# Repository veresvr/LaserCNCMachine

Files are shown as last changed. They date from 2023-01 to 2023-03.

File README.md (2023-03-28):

# Laser CNC Machine

This machine is not something special, just DIY.
Firstly I planned to use a laser but its so easy, so I decided to build milling carriage, like [this](https://github.com/veresvr/SpindleCarriageForCNC).
Also here is [Control Box](https://github.com/veresvr/CNC-Control-Box) for it.<br>
BOM and drawings for the machine [here](https://github.com/veresvr/LaserCNCMachine/tree/main/ProductionFiles/LaserCNCMachine.pdf).



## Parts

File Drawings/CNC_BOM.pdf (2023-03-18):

| Project CNC machine Project Link GitHub (https://github.com/veresvr/LaserCNCMachine) Title cnc_laser_v1.0.SLDASM Project Number CNC.00.00 Designer Vladimir Tyrkin Drawn by Vladimir Tyrkin File CNC_BOM.xlsx Date 18 March 2023
Dwg. | Item No. | Qty | Description | Material | Manufacturer | Part Number | Manufacturer Link | Weight | Total Weight
CNC.01.01 | | 3 | Structural Aluminum Profile 2040 | 6063-T5 | McMaster-Carr | 5537T111-5537T107 | McMaster-Carr (https://www.mcmaster.com/5537T111-5537T107/) | 346 | 1038
| | | | | Soberizavod | 224SHX | Soberizavod (https://www.soberizavod.ru/catalog/seriya_20_obychnyy_paz/profil_konstruktsionnyy_20kh40sh_bez_pokrytiya/)
CNC.01.11 | | 2 | Structural Aluminum Profile 2020 | 6063-T5 | McMaster-Carr | 5537T514-5537T751 | McMaster-Carr (https://www.mcmaster.com/5537T514-5537T751/) | 169 | 338
| | | | | Soberizavod | 222SHX | Soberizavod (https://www.soberizavod.ru/catalog/seriya_20_obychnyy_paz/profil_konstruktsionnyy_20kh20sh_bez_pokrytiya/)
CNC.01.21 | | 1 | Frame Base Y | 6063-T5 | McMaster-Carr | 4630T124 | McMaster-Carr (https://www.mcmaster.com/4630T124/) | 43.77 | 43.77
CNC.01.22-1 | | 1 | Frame Base Mount Bracket Y Without Hole | 6061 Alloy | McMaster-Carr | 9146T14-9146T141 | McMaster-Carr (https://www.mcmaster.com/9146T14-9146T141/) | 7.97 | 7.97
CNC.01.22-2 | | 1 | Frame Base Mount Bracket Y With Hole | 6061 Alloy | McMaster-Carr | 9146T14-9146T142 | McMaster-Carr (https://www.mcmaster.com/9146T14-9146T141/) | 7.9 | 7.9
CNC.02.25 | | 4 | Threaded Rod | Alloy Steel | McMaster-Carr | 94595A235 | McMaster-Carr (https://www.mcmaster.com/94595A235/) | 2.16 | 8.64
CNC.01.02-1 | | 2 | Foot | Polycarbonate Sheet | McMaster-Carr | 8574K281 | McMaster-Carr (https://www.mcmaster.com/8574K281/) | 32.67 | 65.34
CNC.01.02-2 | | 1 | Foot | Polycarbonate Sheet | McMaster-Carr | 8574K281 | McMaster-Carr (https://www.mcmaster.com/8574K281/) | 32.67 | 32.67
CNC.01.02-3 | | 1 | Foot | Polycarbonate Sheet | McMaster-Carr | 8574K281 | McMaster-Carr (https://www.mcmaster.com/8574K281/) | 30.39 | 30.39
CNC.02.42 | | 1 | Adjustment Equipment Part | Polycarbonate Sheet | McMaster-Carr | 8574K281 | McMaster-Carr (https://www.mcmaster.com/8574K281/) | 73.78 | 73.78
CNC.02.41 | | 1 | Stepper Side Part | Polycarbonate Sheet | McMaster-Carr | 8574K281 | McMaster-Carr (https://www.mcmaster.com/8574K281/) | 67.72 | 67.72
CNC.02.44 | | 1 | Equipment Adapter | Polycarbonate Sheet | McMaster-Carr | 8574K281 | McMaster-Carr (https://www.mcmaster.com/8574K281/) | 51.48 | 51.48
CNC.02.21 | | 1 | Right Side Base | Polycarbonate Sheet | McMaster-Carr | 8574K281 | McMaster-Carr (https://www.mcmaster.com/8574K281/) | 99.76 | 99.76
CNC.02.31 | | 1 | Left Side Base | Polycarbonate Sheet | McMaster-Carr | 8574K281 | McMaster-Carr (https://www.mcmaster.com/8574K281/) | 104.4 | 104.4
CNC.02.22 | | 8 | Wheel Spacer 1 | 6061-T6 (SS) | McMaster-Carr | 4634T36 | McMaster-Carr (https://www.mcmaster.com/4634T36/) | 1.12 | 8.96
CNC.01.31 | | 4 | Corner For Sensor | 6060 Alloy | McMaster-Carr | 5585N13-5585N117 | McMaster-Carr (https://www.mcmaster.com/5585N13-5585N117/) | 2.49 | 9.96
CNC.02.24 | | 2 | Corner Bracket For Cable Chain | 6060 Aluminum | McMaster-Carr | 5585N19-5585N137 | McMaster-Carr (https://www.mcmaster.com/5585N19-5585N137/) | 5 | 10
CNC.02.43 | | 8 | Wheel Spacer 2 | 6061-T6 (SS) | McMaster-Carr | 4634T36 | McMaster-Carr (https://www.mcmaster.com/4634T36/) | 1.37 | 10.96
CNC.02.51 | | 1 | Frame Base X | 6063-T5 | McMaster-Carr | 4630T124 | McMaster-Carr (https://www.mcmaster.com/4630T124/) | 17.7 | 17.7
CNC.02.52 | | 1 | Frame Base Mount Bracket X | 6061 Alloy | McMaster-Carr | 9146T15-9146T151 | McMaster-Carr (https://www.mcmaster.com/9146T15-9146T151/) | 6.75 | 6.75
CNC.02.60 | | 1 | Equipment Cable Carrier | Nylon | Aliexpress | none | Aliexpress (https://aliexpress.ru/item/32737987887.html?_ga=2.220930584.1029082422.1628014899-) | 21.86 | 21.86
CNC.03.00 | | 1 | Cable Carrier | Nylon | Aliexpress | none | Aliexpress (https://aliexpress.ru/item/32737987887.html?_ga=2.232483359.1029082422.1628014899-) | 21.86 | 21.86
CNC.04.05-1 | | 1 | Cable label X | Acrylic | Aliexpress | none | Aliexpress (https://aliexpress.ru/item/1005002110837854.html?sku_id=12000018773424358) | 1.58 | 1.58
CNC.04.05-2 | | 1 | Cable label Y | Acrylic | Aliexpress | none | Aliexpress (https://aliexpress.ru/item/1005002110837854.html?sku_id=12000018773424358) | 1.58 | 1.58
CNC.04.05-4 | | 1 | Cable label PWR | Acrylic | Aliexpress | none | Aliexpress (https://aliexpress.ru/item/1005002110837854.html?sku_id=12000018773424358) | 1.58 | 1.58
CNC.04.05-5 | | 1 | Cable label DATA | Acrylic | Aliexpress | none | Aliexpress (https://aliexpress.ru/item/1005002110837854.html?sku_id=12000018773424358) | 1.58 | 1.58
CNC.05.01-1 | | 2 | T-slot Table Plate | 6105 Alloy | Soberizavod | TL1 | Soberizavod (https://www.soberizavod.ru/catalog/profil_dlya_stola_anodirovannyj/profil_dlya_stola_legkiy_11kh75_an_serebro/) | 541.63 | 1083.3
CNC.05.01-2 | | 2 | T-slot Table Plate | 6105 Alloy | Soberizavod | TL1 | Soberizavod (https://www.soberizavod.ru/catalog/profil_dlya_stola_anodirovannyj/profil_dlya_stola_legkiy_11kh75_an_serebro/) | 541.8 | 1083.6
CNC.05.01-3 | | 1 | T-slot Table Plate | 6105 Alloy | Soberizavod | TL1 | Soberizavod (https://www.soberizavod.ru/catalog/profil_dlya_stola_anodirovannyj/profil_dlya_stola_legkiy_11kh75_an_serebro/) | 377.6 | 377.6
CNC.05.05 | | 2 | Corner Braket Long | 6061 Alloy | McMaster-Carr | 5585N18-5585N134 | McMaster-Carr (https://www.mcmaster.com/5585N18-5585N134/) | 117.04 | 234.08
CNC.02.11 | | 1 | Rotary Shaft | AISI 1020 | McMaster-Carr | 8920K18-8920K183 | McMaster-Carr (https://www.mcmaster.com/8920K18-8920K183/) | 61.66 | 61.66
None | | 4 | Corner Bracket 40х20L | AISI 1035 Steel (SS) | Soberizavod | H49 | Soberizavod (https://www.soberizavod.ru/catalog/uglovye_soediniteli_seriya_20/ugolok_40kh20l_paz_6_h49/) | 49 | 196
None | | 8 | Corner Bracket 20х20L | Steel | Soberizavod | none | Soberizavod (https://www.soberizavod.ru/catalog/uglovye_soediniteli_seriya_20/ugolok_20kh20l_paz_6_m51/) | 10.14 | 81.12
| | | | Anodized 6063 Aluminum | McMaster-Carr | 5537T935 | McMaster-Carr (https://www.mcmaster.com/5537T935/)
None | | 1 | LASER 5500mW | Multimaterial | Aliexpress | none | Aliexpress (https://aliexpress.ru/item/32807131516.html?mp=1&_ga=2.210714258.625657640.1626994396-) | 400 | 400
None | | 4 | Limit Switch | Multimaterial | DIGIKEY | none | DIGIKEY (https://www.digikey.com/en/products/detail/omron-electronics-inc-emc-div/ssg-01l2t-5/3102941) | 1.6 | 6.4
| | | | Multimaterial | Aliexpress | none | Aliexpress (https://aliexpress.ru/item/32820271171.html?_ga=2.96440341.847069604.1626648373-)
None | | 2 | Nema 17HS4401 Stepper Motor | Multimaterial | Aliexpress | none | Aliexpress (https://aliexpress.ru/item/32665922113.html?_ga=2.134133639.847069604.1626648373-) | 315 | 630
None | | 12 | Cable Tie Plastic | Nylon 101 | McMaster-Carr | 7130K12 | McMaster-Carr (https://www.mcmaster.com/7130K12/) | 0.18 | 2.16
None | | 3 | Timing Belt 430mm | Rubber | Aliexpress | none | Aliexpress (https://aliexpress.ru/item/32619587350.html?_ga=2.189989419.1029082422.1628014899-) | 3.98 | 11.94
| | | Timing Belt 430mm | Rubber | McMaster-Carr | 3682N1-3682N13 | McMaster-Carr (https://www.mcmaster.com/3682N1-3682N13/)
None | | 3 | GX16-4P cable female | Multimaterial | Aliexpress | none | Aliexpress (https://aliexpress.ru/item/32776129751.html?_ga=2.152725433.1029082422.1628014899-) | 10 | 30
None | | 3 | Pulley GT2-12 | Multimaterial | Aliexpress | none | Aliexpress (https://aliexpress.ru/item/32871142006.html?_ga=2.137935673.847069604.1626648373-) | 1.23 | 3.69
Page 1 of 2 | 3/18/2023 14:22

Dwg. | Item No. | Qty | Description | Material | Manufacturer | Part Number | Manufacturer Link
Weight

Total
Weight
None | 1 | Flexible shaft coupling 5x5 | Multimaterial | Aliexpress | none | Aliexpress (https://aliexpress.ru/item/32619555244.html?_ga=2.139041594.847069604.1626648373-) | 16.06 | 16.06
None | 1 | Connector D-SUB 9 Male | Multimaterial | MOUSER | none | Mouser (https://eu.mouser.com/ProductDetail/HARTING/09641227230?qs=qa49y27LPCEuVI2dYdFOjA%3D%3D) | 5 | 5
None | 1 | Connector PG11 | ABS | Amazon | none | Amazon (https://www.amazon.com/White-Plastic-Waterproof-Glands-Connectors/dp/B00843UH4O) | 12.38 | 12.38
None | 1 | Cable Holder | ABS | Soberizavod | none | Soberizavod (https://www.soberizavod.ru/catalog/zaglushki_dlya_paza/zaglushka_dlya_paza_6_mm_chernaya_z15/) | 3.07 | 3.07
None | 1 | Heat-Shrink Tubing 1 (Length 110mm) | Rubber | Digikey | ATU031K-ND | Digikey (https://www.digikey.com/en/products/detail/te-connectivity-raychem-cable-protection/ATUM-3-1-0-STK/573461) | 0 | 0
None | 1 | Heat-Shrink Tubing 2 (Length 25mm) | Rubber | Digikey | SCT-NO.2-E5-0-12MMND | Digikey (https://www.digikey.com/en/products/detail/te-connectivity-raychem-cable-protection/SCT-NO-2-E5-0-12MM/5318099) | 0 | 0
Total weight | 6322.2

3D printed parts

CNC.02.23 | 1 | Spacer for stepper | PET-G | McMaster-Carr | 3462N1 | McMaster-Carr (https://www.mcmaster.com/3462N1/) | 20.9 | 20.9
| | File: ProductionFiles/SpacerForStepper.STL
CNC.02.45 | 2 | Carriage Spacer | PET-G | McMaster-Carr | 3462N1 | McMaster-Carr (https://www.mcmaster.com/3462N1/) | 5.49 | 10.98
| | File: ProductionFiles/CarriageSpacer.STL
Total weight | 31.88
Screws
None | 4 | Head screw ISO 7380 M5 x 50 | AISI 304 | Aliexpress | none | Aliexpress (https://aliexpress.ru/item/32966917947.html?_ga=2.131725446.847069604.1626648373-) | 8.84 | 35.36
None | 56 | M3 NYLOC DIN 985 | AISI 304 | Aliexpress | 500214 | Aliexpress (https://www.mcmaster.com/nuts/locknuts/metric-18-8-stainless-steel-nylon-insert-locknuts/) | 0.4 | 22.4
None | 6 | Square nut M5 | Zinc-Plated Steel | Soberizavod | A209 | Soberizavod (https://www.soberizavod.ru/catalog/sukhari_pazovye_paz_6/sukhar_pazovyy_ploskiy_m5_paz_6_a209/) | 1.84 | 11.04
| | | Zinc-Plated Steel | McMaster-Carr | 5537t161 | McMaster-Carr (https://www.mcmaster.com/5537t161/)
None | 20 | M5 NYLOC DIN 985 | AISI 304 | McMaster-Carr | 5100214 | McMaster-Carr (https://www.mcmaster.com/nuts/locknuts/metric-18-8-stainless-steel-nylon-insert-locknuts/) | 1.1 | 22
None | 4 | Low Profile Hex Screw M5x30 | Alloy Steel | Aliexpress | none | Aliexpress (https://aliexpress.ru/item/4001232036314.html?_ga=2.27484988.1065263870.1623483208-) | 5.27 | 21.08
| | | Alloy Steel | McMaster-Carr | none | McMaster-Carr (https://www.mcmaster.com/90358A119/)
None | 8 | Head screw ISO 7380 M5 x 35 | AISI 304 | Aliexpress | none | Aliexpress (https://aliexpress.ru/item/32966917947.html?_ga=2.9302450.625657640.1626994396-) | 5.08 | 40.64
None | 6 | Head screw ISO 7380 M5 x 6 | 18-8 Stainless Steel | Aliexpress | none | Aliexpress (https://aliexpress.ru/item/32966917947.html?_ga=2.159815732.847069604.1626648373-) | 2 | 12
None | 20 | ISO 10642 - M3 x 16 - 16N | 18-8 Stainless Steel | McMaster-Carr | none | McMaster-Carr (https://www1.mcmaster.com/screws/flat-head-screws/phillips-flat-head-screws/metric-18-8-stainless-steel-phillips-flat-head-screws/) | 0.47 | 9.4
None | 24 | Head screw ISO 7380 M5 x 8 | 18-8 Stainless Steel | McMaster-Carr | 91292A121 | McMaster-Carr (https://www.mcmaster.com/94500A230/) | 2 | 48
| | | 18-8 Stainless Steel | Aliexpress | none | Aliexpress (https://aliexpress.ru/item/32953923124.html?_ga=2.138868666.847069604.1626648373-)
None | 16 | Washer DIN 125 - A 5.3 | Zinc Plated Steel | McMaster-Carr | 91166A240 | McMaster-Carr (https://www1.mcmaster.com/91166A240/) | 0.44 | 7.04
None | 32 | T nut 2020 М5 | 316 Stainless Steel | Aliexpress | none | Aliexpress (https://aliexpress.ru/item/32955951597.html?spm=a2g0s.9042311.0.0.274233ed1qtpPS) | 2.08 | 66.56
None | 4 | Washer DIN 125 - A 3.2 | Zinc Plated Steel | McMaster-Carr | 91166A210 | McMaster-Carr (https://www1.mcmaster.com/91166A210/) | 0.12 | 0.48
None | 14 | ISO 4762 M3 x 8 - 8N | Zinc Plated Steel | McMaster-Carr | 91502A103 | McMaster-Carr (https://www.mcmaster.com/91502A103/) | 0.8 | 11.2
None | 14 | ISO 4762 M3 x 12 - 12N | 18-8 Stainless Steel | McMaster-Carr | none | McMaster-Carr (https://www.mcmaster.com/screws/socket-head-screws/socket-head-screws-6/18-8-stainless-steel-socket-head-screws-11/system-of-measurement~metric/) | 1.16 | 16.24
None | 8 | ISO 7380 - M5 x 10 - 10N | 316 Stainless Steel | McMaster-Carr | 90943A117 | McMaster-Carr (https://www.mcmaster.com/90943A117/) | 2.09 | 16.72
None | 4 | ISO 7380 - M5 x 16 - 16N | 18-8 Stainless Steel | McMaster-Carr | 92095A212 | McMaster-Carr (https://www.mcmaster.com/92095A212/) | 2.9 | 11.6
None | 16 | ISO 7380 - M3 x 8 - 8N | 18-8 Stainless Steel | McMaster-Carr | 92095A181 | McMaster-Carr (https://www1.mcmaster.com/92095A181/) | 0.6 | 9.6
None | 12 | ISO 4762 M6 x 20 - 20N | Zinc-Plated Steel | McMaster-Carr | 90128A264 | McMaster-Carr (https://www.mcmaster.com/90128A264/) | 6.53 | 78.36
None | 4 | ISO 4762 M4 x 6 - 6N | Zinc-Plated Steel | McMaster-Carr | 90128A208 | McMaster-Carr (https://www.mcmaster.com/90128A208/) | 3.7 | 14.8
None | 4 | Head screw ISO 7380 M3 x 16 | AISI 304 | Aliexpress | none | Aliexpress (https://www1.mcmaster.com/92005A120/) | 1 | 4
None | 1 | Stainless Steel Ball Bearing 625-2Z (ISO 15 RBB - 025 - 8,DE,NC,8_68) | Multimaterial | McMaster-Carr | 6153K15 | McMaster-Carr (https://www.mcmaster.com/6153K15/) | 5.6 | 5.6
Total weight | 464.12
Cables
None | 1 | Stepper X Cable ( Control Cable 1850mm) | Multimaterial | McMaster-Carr | 6650T12 | McMaster-Carr (https://www.mcmaster.com/6650T12/) | 50 | 50
None | 1 | Stepper Y Cable ( Control Cable 2900mm) | Multimaterial | McMaster-Carr | 6650T12 | McMaster-Carr (https://www.mcmaster.com/6650T12/) | 50 | 50
None | 1 | Power Cable ( Power Supply Cable 3200mm) | Multimaterial | McMaster-Carr | 7394K31 | McMaster-Carr (https://www.mcmaster.com/7394K31/) | 50 | 50
None | 1 | Data Cable ( Multiple Conductor Cable 1040mm) | Multimaterial | Digikey | T1430-153-ND | Digikey (https://www.digikey.com/en/products/detail/tensility-international-corp/30-01331/10292905) | 50 | 50
| | | Multimaterial | McMaster-Carr | 6650T14 | McMaster-Carr (https://www.mcmaster.com/6650T14/) | | 0
None | 1 | Hook-Up Wire ( Wire 5300mm) | Multimaterial | Digikey | FLTWC0311-26-9-ND | Digikey (https://www.digikey.com/en/products/detail/te-connectivity-raychem-cable-protection/FLTWC0311-26-9/5330221) | 50 | 50
Total weight | 250
All project weight | 7068.2
Page 2 of 2 | 3/18/2023 14:22

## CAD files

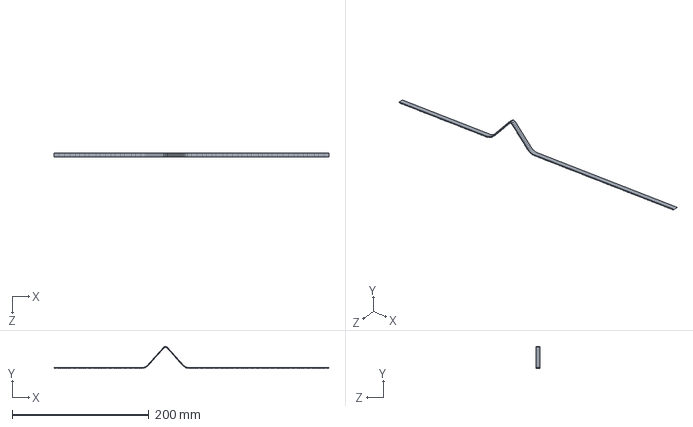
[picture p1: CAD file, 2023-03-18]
3D/TimingBelt2.SLDASM
402.8 x 32.5 x 6.00 mm
PartOfBeltP2W6^TimingBelt2 x 214

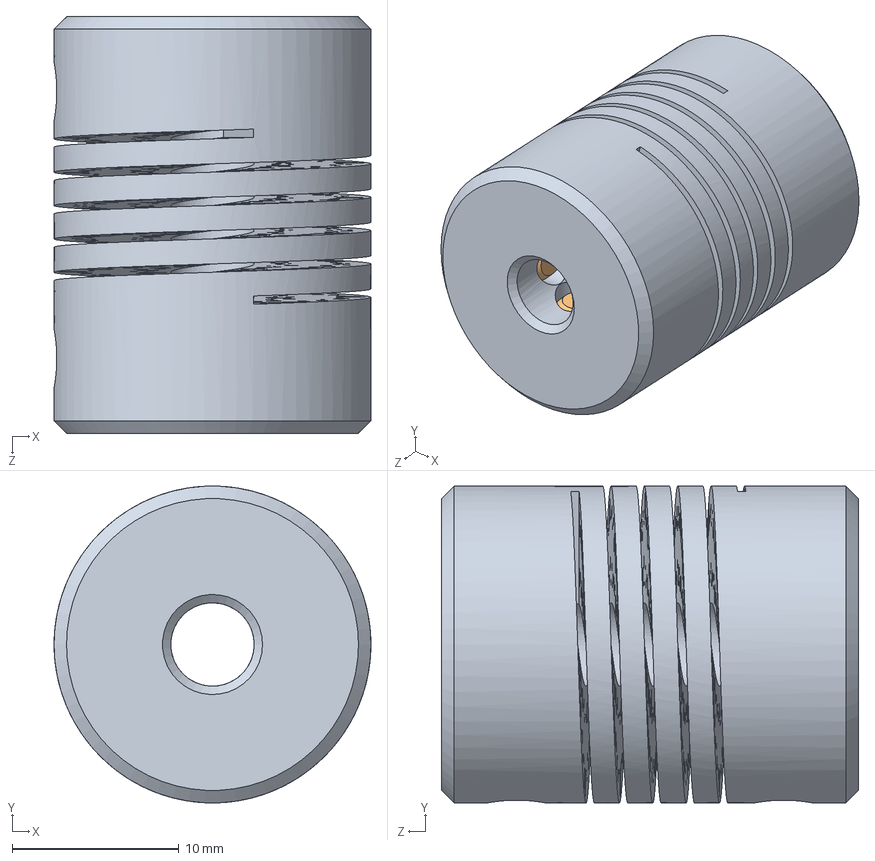
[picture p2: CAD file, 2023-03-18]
3D/Flexible shaft coupling 5x5.SLDASM
19.0 x 19.0 x 25.0 mm
Flexible Jaw Shaft Coupling^Flexible shaft coupling 5x5
socket set screw flat point_iso x 4

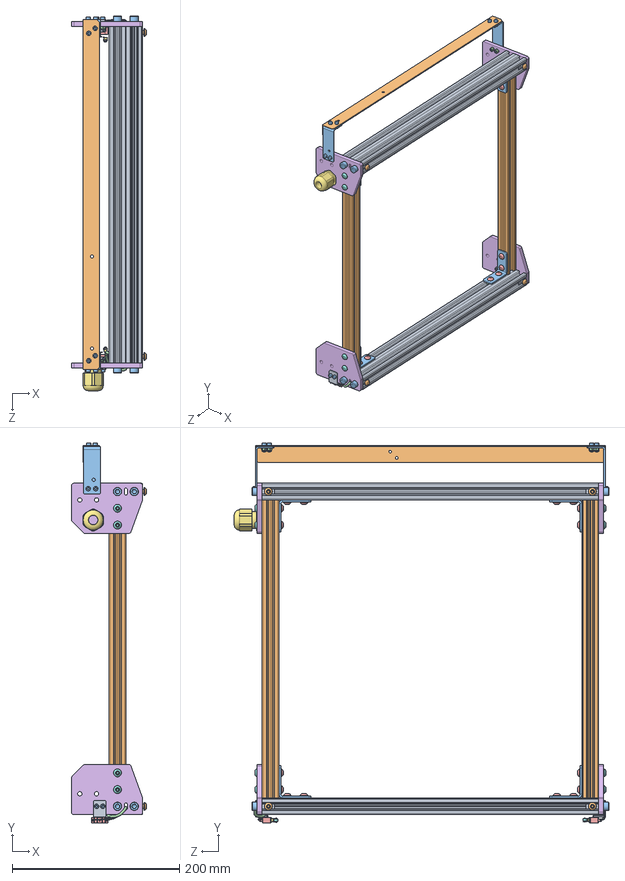
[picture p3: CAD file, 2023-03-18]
3D/BaseFrameAssembly.SLDASM
89.7 x 453.9 x 447.4 mm
Structural Aluminum Profile 2040 x 2
Structural Aluminum Profile 2020 x 2
Corner Bracket 40х20L x 4
T nut 2020 М5 x 24
head screw ISO 7380 M5 x 8 x 16
Foot x 4
IEK_PGxx
socket button head screw_iso x 8
Square nut M5 x 4
head screw ISO 7380 M5 x 6 x 4
socket head cap screw_iso x 24
Nyloc nut St_Steel A2 ISO M2_5-M36 x 12
Body^Limit Switch x 2
Wheel shaft^Limit Switch x 2
Link^Limit Switch x 2
Wheel^Limit Switch x 2
CornerForSensor x 2
FrameBaseY
FrameBaseMountBracketY x 2
CableEndSensor1^BaseFrameAssembly

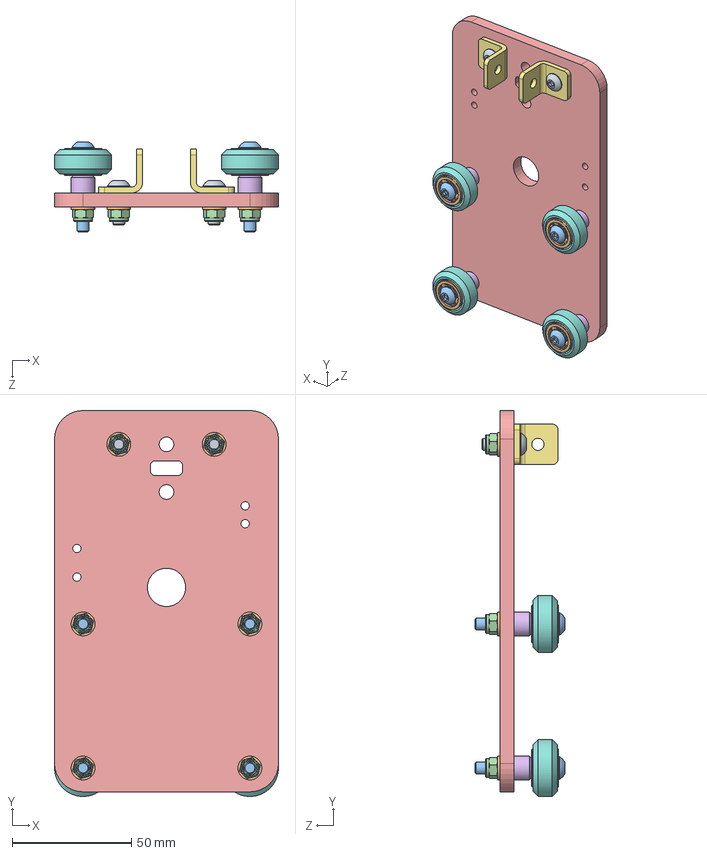
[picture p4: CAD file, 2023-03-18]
3D/LeftSideCarriage.SLDASM
94.0 x 161.9 x 37.8 mm
socket button head screw_iso x 2
plain washer grade a_din x 6
head screw ISO 7380 M5 x 35 x 4
Nyloc nut St_Steel A2 ISO M2_5-M36 x 6
LeftSideBase
WheelSpacer1 x 4
Corner Bracket 20х20L x 2
PlasticWheel^Solid V-Wheel D=24 d=5 x 4
Spacer 1mm^Solid V-Wheel D=24 d=5 x 4
radial ball bearing_68_iso x 8

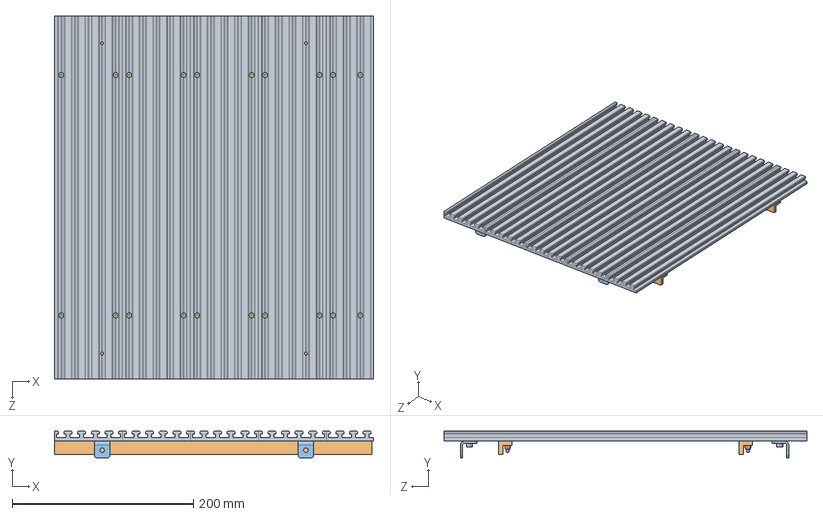
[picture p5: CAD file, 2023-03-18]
3D/TableTSlot.SLDASM
351.6 x 29.5 x 400.0 mm
T-slot Table Plate x 5
CornerBraketLong x 2
Corner Bracket 20х20L x 4
socket countersunk head screw_iso x 20
socket head cap screw_iso x 4
Nyloc nut St_Steel A2 ISO M2_5-M36 x 20

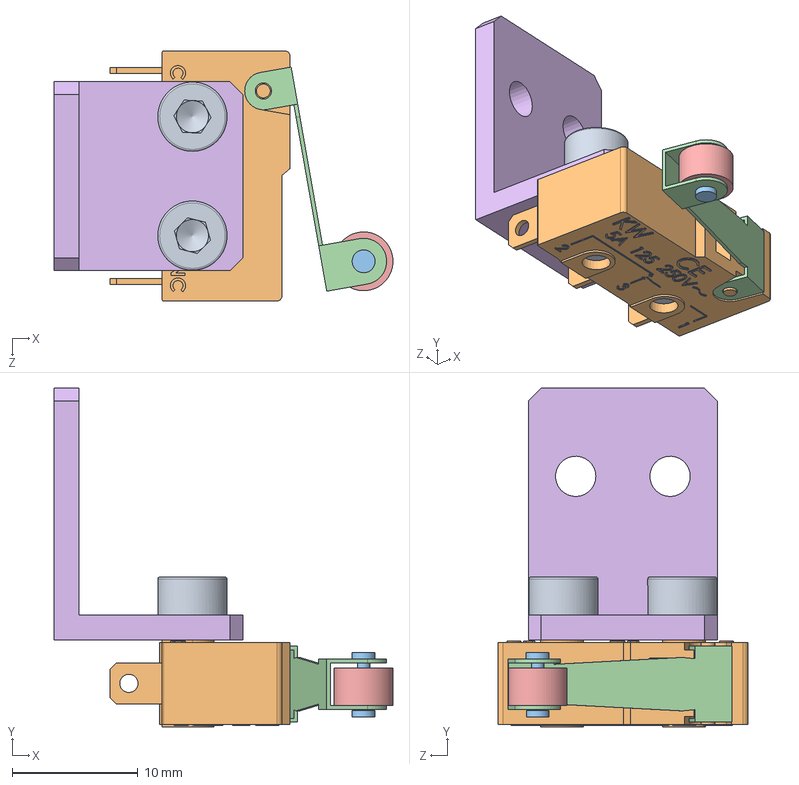
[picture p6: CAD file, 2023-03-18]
3D/LimitSwitch.SLDASM
26.9 x 26.9 x 19.9 mm
socket head cap screw_iso x 2
Body^Limit Switch
Wheel shaft^Limit Switch
Link^Limit Switch
Wheel^Limit Switch
CornerForSensor

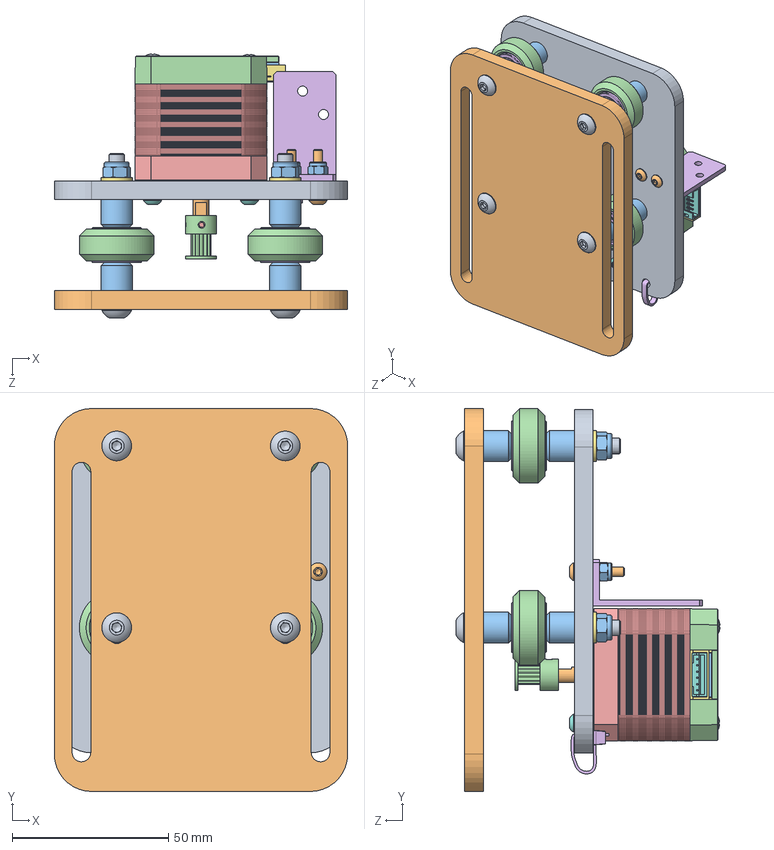
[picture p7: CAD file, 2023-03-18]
3D/Equipment Carriage.SLDASM
94.0 x 122.7 x 84.6 mm
Stepper Side Part
Adjustment Equipment Part
Wheel Spacer 2 x 8
PlasticWheel^Solid V-Wheel D=24 d=5 x 4
Spacer 1mm^Solid V-Wheel D=24 d=5 x 4
radial ball bearing_68_iso x 8
plain washer grade a_din x 4
socket button head screw_iso x 4
head screw ISO 7380 M5 x 4
head screw ISO 7380 M3 x 16 x 2
Nyloc nut St_Steel A2 ISO M2_5-M36 x 6
GT2-12_А1110^Pulley GT2-12
socket set screw cup point_iso x 2
CornerBracketForCableChain
BS 3469 - 02 - 5 x 16 x 5^Nema 17HS4401 Stepper Motor x 2
Nema 17 Plastic Spacer 2^Nema 17HS4401 Stepper Motor
Nema 17 Plastic Spacer 1
Nema 17 shaft^Nema 17HS4401 Stepper Motor
ANSI B27.7 - 5, E^Nema 17HS4401 Stepper Motor
Nema 17 Base Cap^Nema 17HS4401 Stepper Motor
Nema 17 Central Spacer^Nema 17HS4401 Stepper Motor
Nema 17 Stator Face^Nema 17HS4401 Stepper Motor
Nema 17 plastic^Nema 17HS4401 Stepper Motor
S6B-PH-K-S^Nema 17HS4401 Stepper Motor
EN ISO 7045 - M3 x 25(1)^Nema 17HS4401 Stepper Motor x 4
Nema 17 plastic protector^Nema 17HS4401 Stepper Motor
Nema 17 PCB^Nema 17HS4401 Stepper Motor
Nema 17 Sprung Washer^Nema 17HS4401 Stepper Motor
17HS4401-Part5^Nema 17HS4401 Stepper Motor
cableTiePlastic

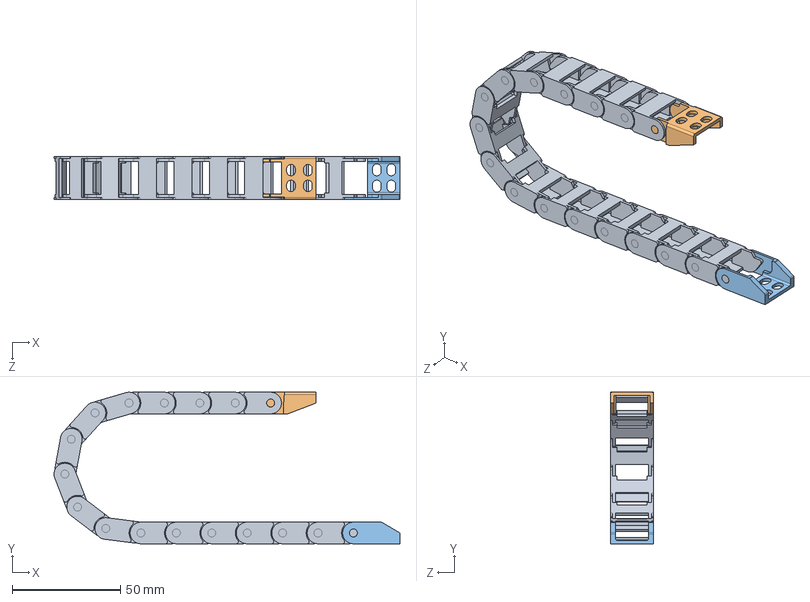
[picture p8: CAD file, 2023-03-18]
3D/CableCarrier.SLDASM
159.7 x 70.0 x 20.0 mm
CableChainSection x 16
CarrierPartMale
CarrierPartFemale

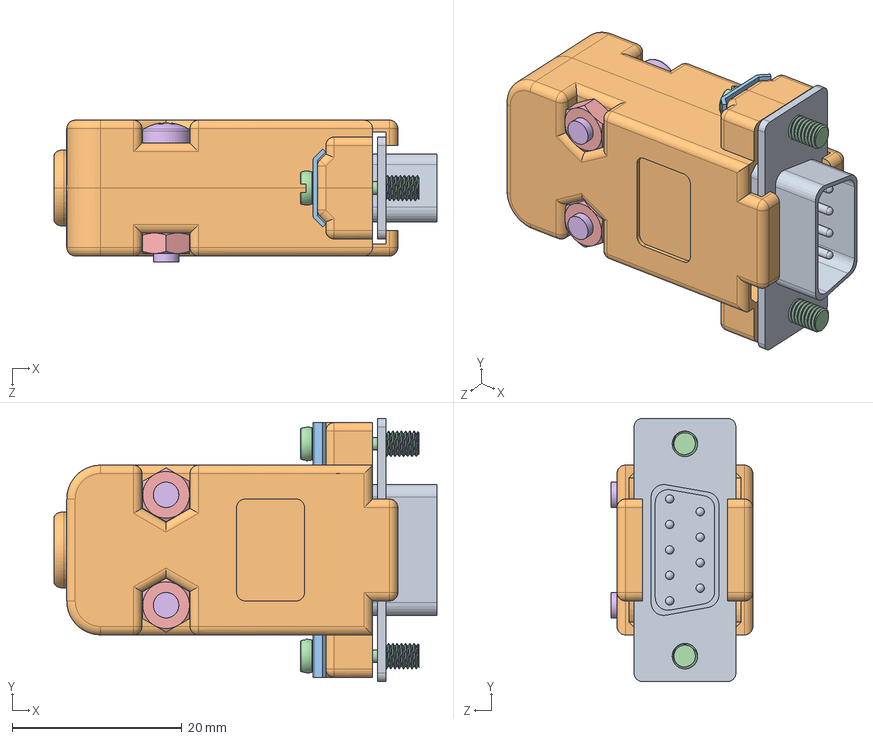
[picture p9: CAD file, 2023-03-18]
3D/DSub connector plastic cover.SLDASM
45.1 x 31.0 x 16.7 mm
d-sub9_male^DSub connector plastic cover
PartPlasticCover^DSub connector plastic cover x 2
ClampPlasticCover^DSub connector plastic cover x 2
ScrewPlasticCover^DSub connector plastic cover x 2
hex nut style 1 gradeab_iso x 2
pan head cross recess screw_iso7045 x 2

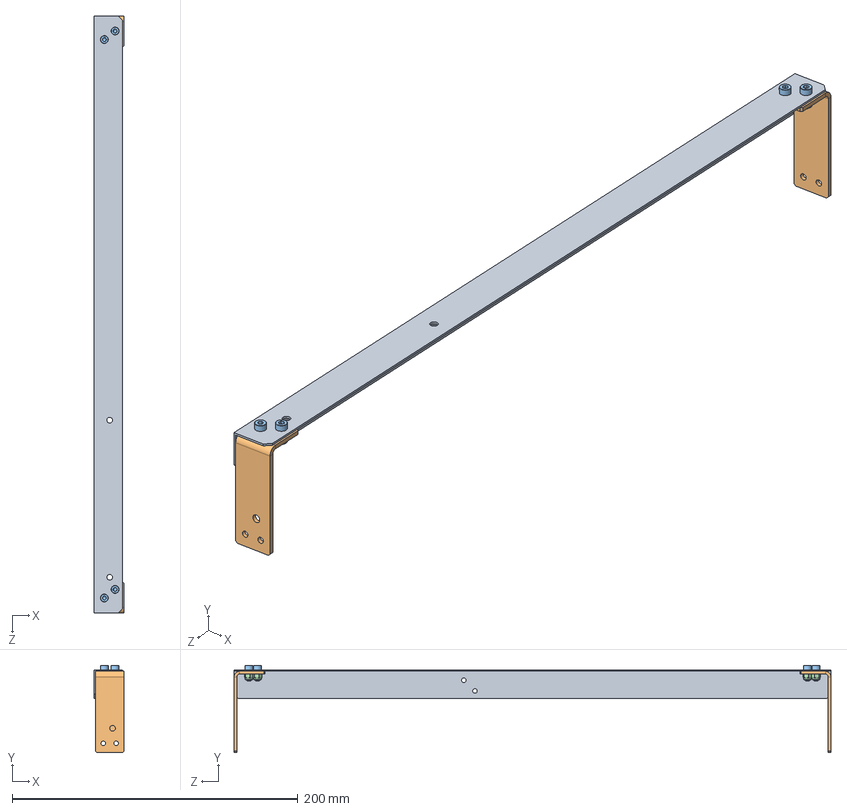
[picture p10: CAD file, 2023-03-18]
3D/CableChainMountFrameY.SLDASM
21.0 x 60.9 x 418.0 mm
FrameBaseY
FrameBaseMountBracketY x 2
socket head cap screw_iso x 4
Nyloc nut St_Steel A2 ISO M2_5-M36 x 4

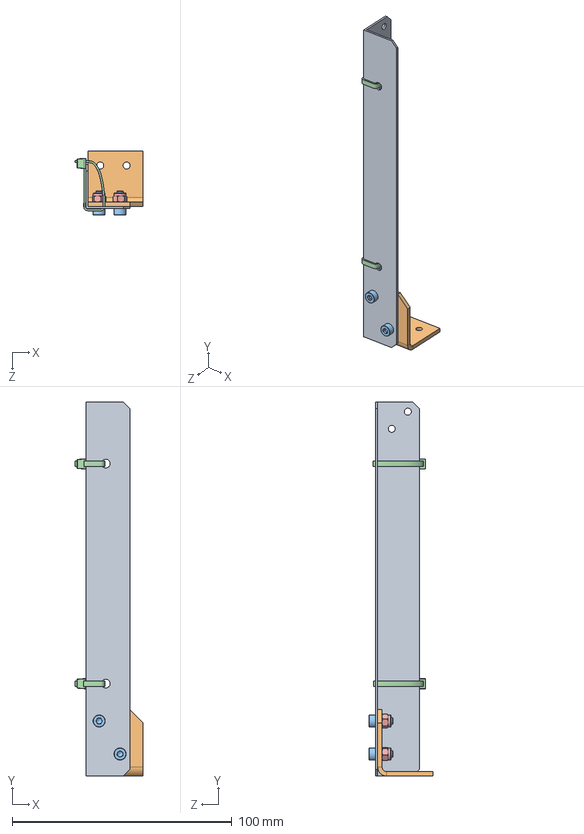
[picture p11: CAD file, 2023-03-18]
3D/CableChainMountFrameX.SLDASM
31.0 x 170.0 x 29.1 mm
Frame Base X
FrameBaseMountBracketX
socket head cap screw_iso x 2
cableTiePlastic x 2
Nyloc nut St_Steel A2 ISO M2_5-M36 x 2

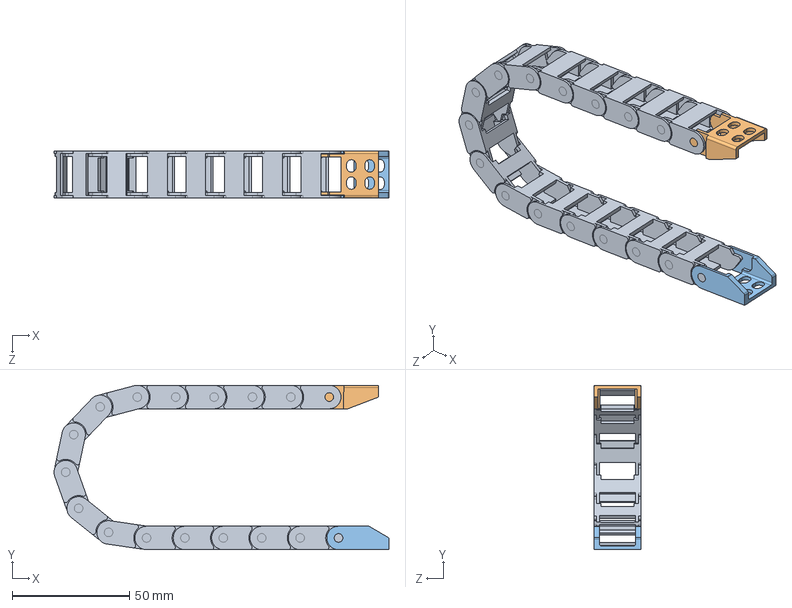
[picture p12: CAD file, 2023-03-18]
3D/EquipmentCableCarrier.SLDASM
142.7 x 70.0 x 20.0 mm
CableChainSection x 16
CarrierPartMale
CarrierPartFemale

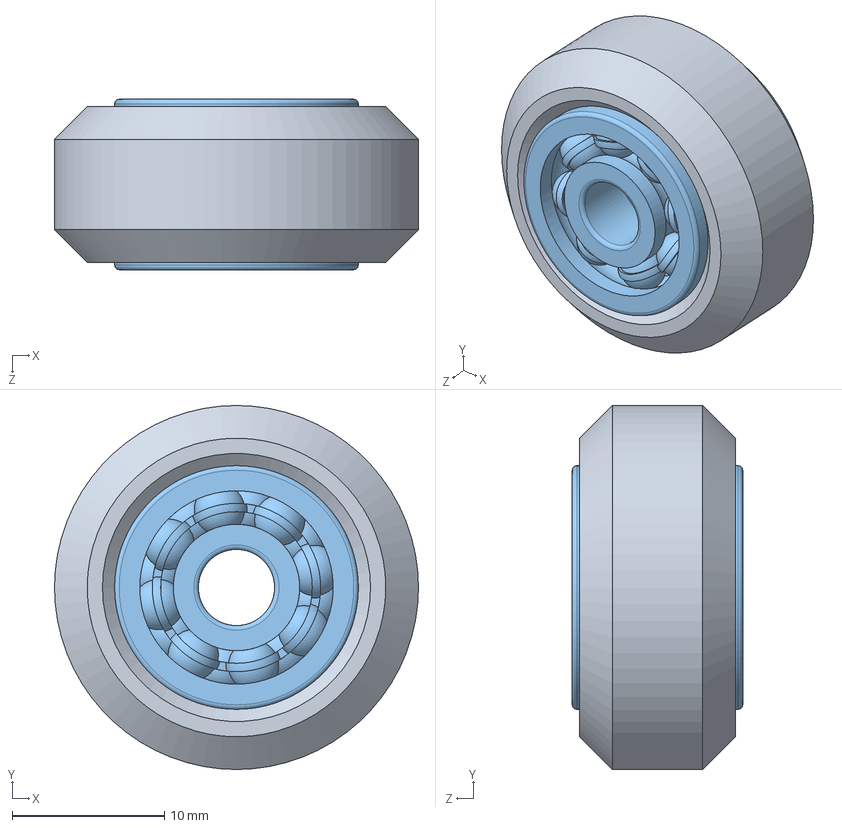
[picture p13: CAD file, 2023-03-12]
3D/Solid V-Wheel D=24 d=5.SLDASM
23.9 x 23.9 x 11.2 mm
PlasticWheel^Solid V-Wheel D=24 d=5
Spacer 1mm^Solid V-Wheel D=24 d=5
radial ball bearing_68_iso x 2

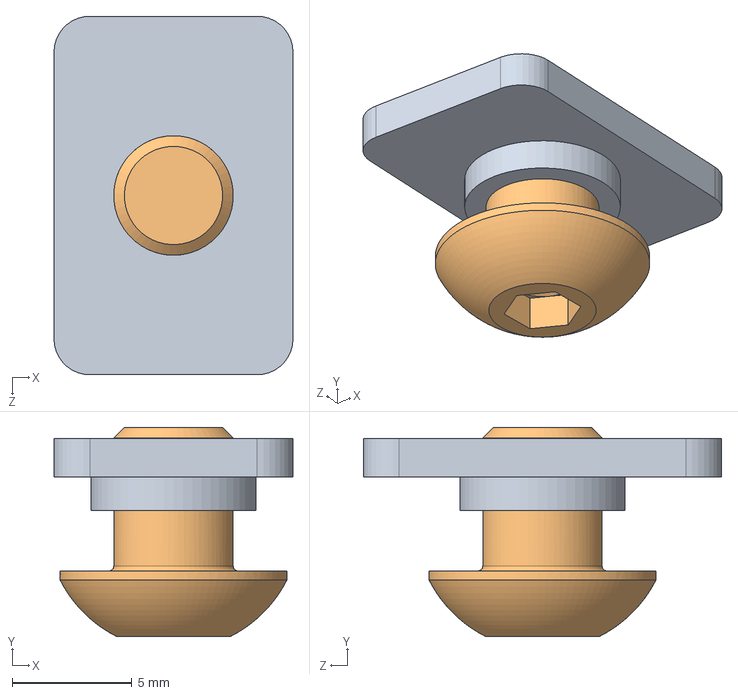
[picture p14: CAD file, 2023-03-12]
3D/BeltLocker.SLDASM
10.0 x 8.75 x 15.0 mm
Square nut M5
head screw ISO 7380 M5 x 6

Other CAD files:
3D/Pulley GT2-12.SLDASM
3D/AssemblyCorner.SLDASM
3D/FootMount.SLDASM
3D/Crossbar.SLDASM
3D/Adjustment Equipment Part.SLDPRT
3D/Cable label.SLDPRT
3D/CableChainSection.SLDPRT
3D/CarriageSpacer.SLDPRT
3D/CarrierPartFemale.SLDPRT
3D/CarrierPartMale.SLDPRT
3D/Conector DB 9 Female.SLDPRT
3D/Corner Bracket 20х20L.SLDPRT
3D/Corner Bracket 40х20L.SLDPRT
3D/CornerBracketForCableChain.SLDPRT
3D/CornerBraketLong.SLDPRT
3D/CornerForSensor.SLDPRT
3D/Equipment Adapter.SLDPRT
3D/Foot.SLDPRT
3D/Frame Base X.SLDPRT
3D/FrameBaseMountBracketX.SLDPRT
3D/FrameBaseMountBracketY.SLDPRT
3D/FrameBaseY.SLDPRT
3D/GX16-4P cable female.SLDPRT
3D/IEK_PGxx.SLDPRT
3D/LASER 5500mW.SLDPRT
3D/LaserUnit.SLDASM
3D/LeftSideBase.SLDPRT
3D/Limit Switch.SLDASM
3D/Low Profile Hex Screw M5x30.SLDPRT
3D/MainCarriageAssembly^cnc_laser_v1.0.SLDASM
3D/Nema 17 Plastic Spacer 1.sldprt
3D/Nyloc nut St_Steel A2 ISO M2_5-M36.SLDPRT
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

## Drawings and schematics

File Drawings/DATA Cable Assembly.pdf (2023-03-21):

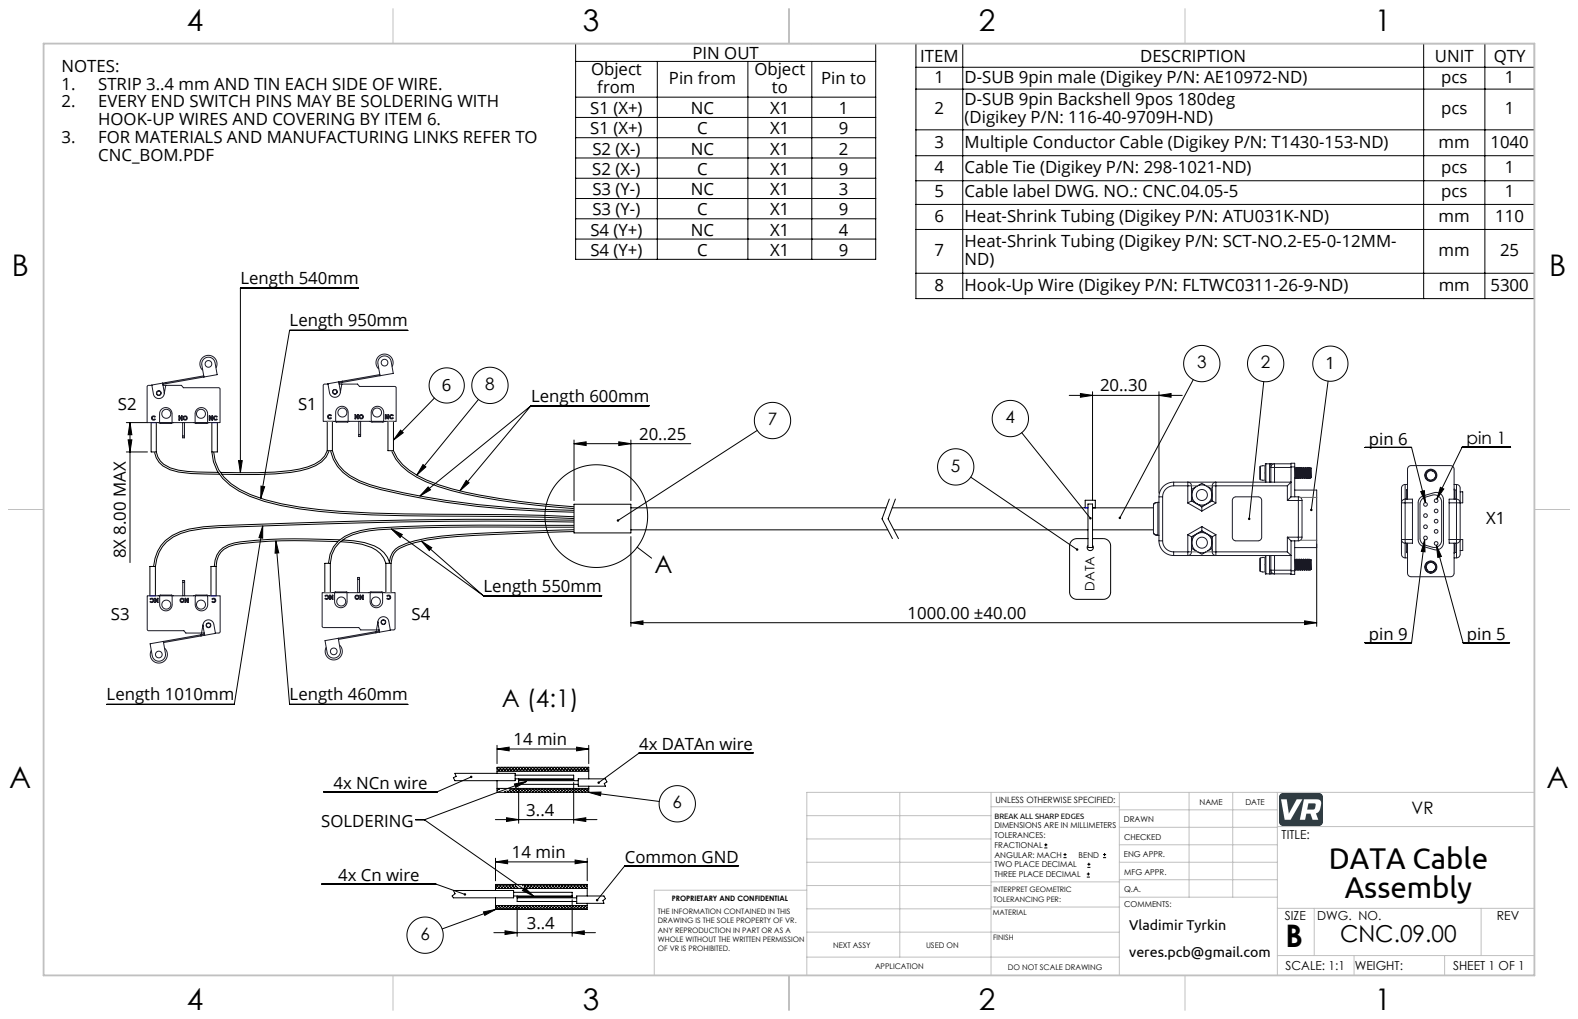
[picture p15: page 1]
14 min; 8X 8.00 MAX; 4x NCn wire; 4x DATAn wire; 4x Cn wire; Common GND; Length 950mm; Length 540mm; Length 600mm; Length 460mm; Length 550mm; Length 1010mm; pin 9; pin 5; pin 6; pin 1; OF VR IS PROHIBITED.; veres.pcb@gmail.com; Vladimir Tyrkin

PIN OUT | | ITEM | DESCRIPTION | UNIT | QTY

NOTES:
1. STRIP 3..4 mm AND TIN EACH SIDE OF WIRE.
2. EVERY END SWITCH PINS MAY BE SOLDERING WITH
HOOK-UP WIRES AND COVERING BY ITEM 6.
3. FOR MATERIALS AND MANUFACTURING LINKS REFER TO
CNC_BOM.PDF

Object from | Pin from | Object to | Pin to
S1 (X+) | NC | X1 | 1
S1 (X+) | C | X1 | 9
S2 (X-) | NC | X1 | 2
S2 (X-) | C | X1 | 9 | | 4 | Cable Tie (Digikey P/N: 298-1021-ND) | pcs | 1
S3 (Y-) | NC | X1 | 3 | | 5 | Cable label DWG. NO.: CNC.04.05-5 | pcs | 1
S3 (Y-) | C | X1 | 9
S4 (Y+) | NC | X1 | 4
S4 (Y+) | C | X1 | 9

1 | D-SUB 9pin male (Digikey P/N: AE10972-ND) | pcs | 1
2 | D-SUB 9pin Backshell 9pos 180deg (Digikey P/N: 116-40-9709H-ND) | pcs | 1

3 | Multiple Conductor Cable (Digikey P/N: T1430-153-ND) | mm | 1040

6 | Heat-Shrink Tubing (Digikey P/N: ATU031K-ND) | mm | 110
7 | Heat-Shrink Tubing (Digikey P/N: SCT-NO.2-E5-0-12MM-ND) | mm | 25

8 | Hook-Up Wire (Digikey P/N: FLTWC0311-26-9-ND) | mm | 5300

UNLESS OTHERWISE SPECIFIED: | | DATE | VR NAME
BREAK ALL SHARP EDGES DIMENSIONS ARE IN MILLIMETERS TOLERANCES: FRACTIONAL ANGULAR: MACH BEND TWO PLACE DECIMAL THREE PLACE DECIMAL | DRAWN

CHECKED | | TITLE: DATA Cable Assembly

ENG APPR.
MFG APPR.

INTERPRET GEOMETRIC TOLERANCING PER: | Q.A.
MATERIAL | | SIZE B | DWG. NO. CNC.09.00 | REV

PROPRIETARY AND CONFIDENTIAL
THE INFORMATION CONTAINED IN THIS
DRAWING IS THE SOLE PROPERTY OF VR.
ANY REPRODUCTION IN PART OR AS A
WHOLE WITHOUT THE WRITTEN PERMISSION

NEXT ASSY | USED ON | FINISH

APPLICATION | DO NOT SCALE DRAWING | | SCALE: 1:1 | WEIGHT: | SHEET 1 OF 1

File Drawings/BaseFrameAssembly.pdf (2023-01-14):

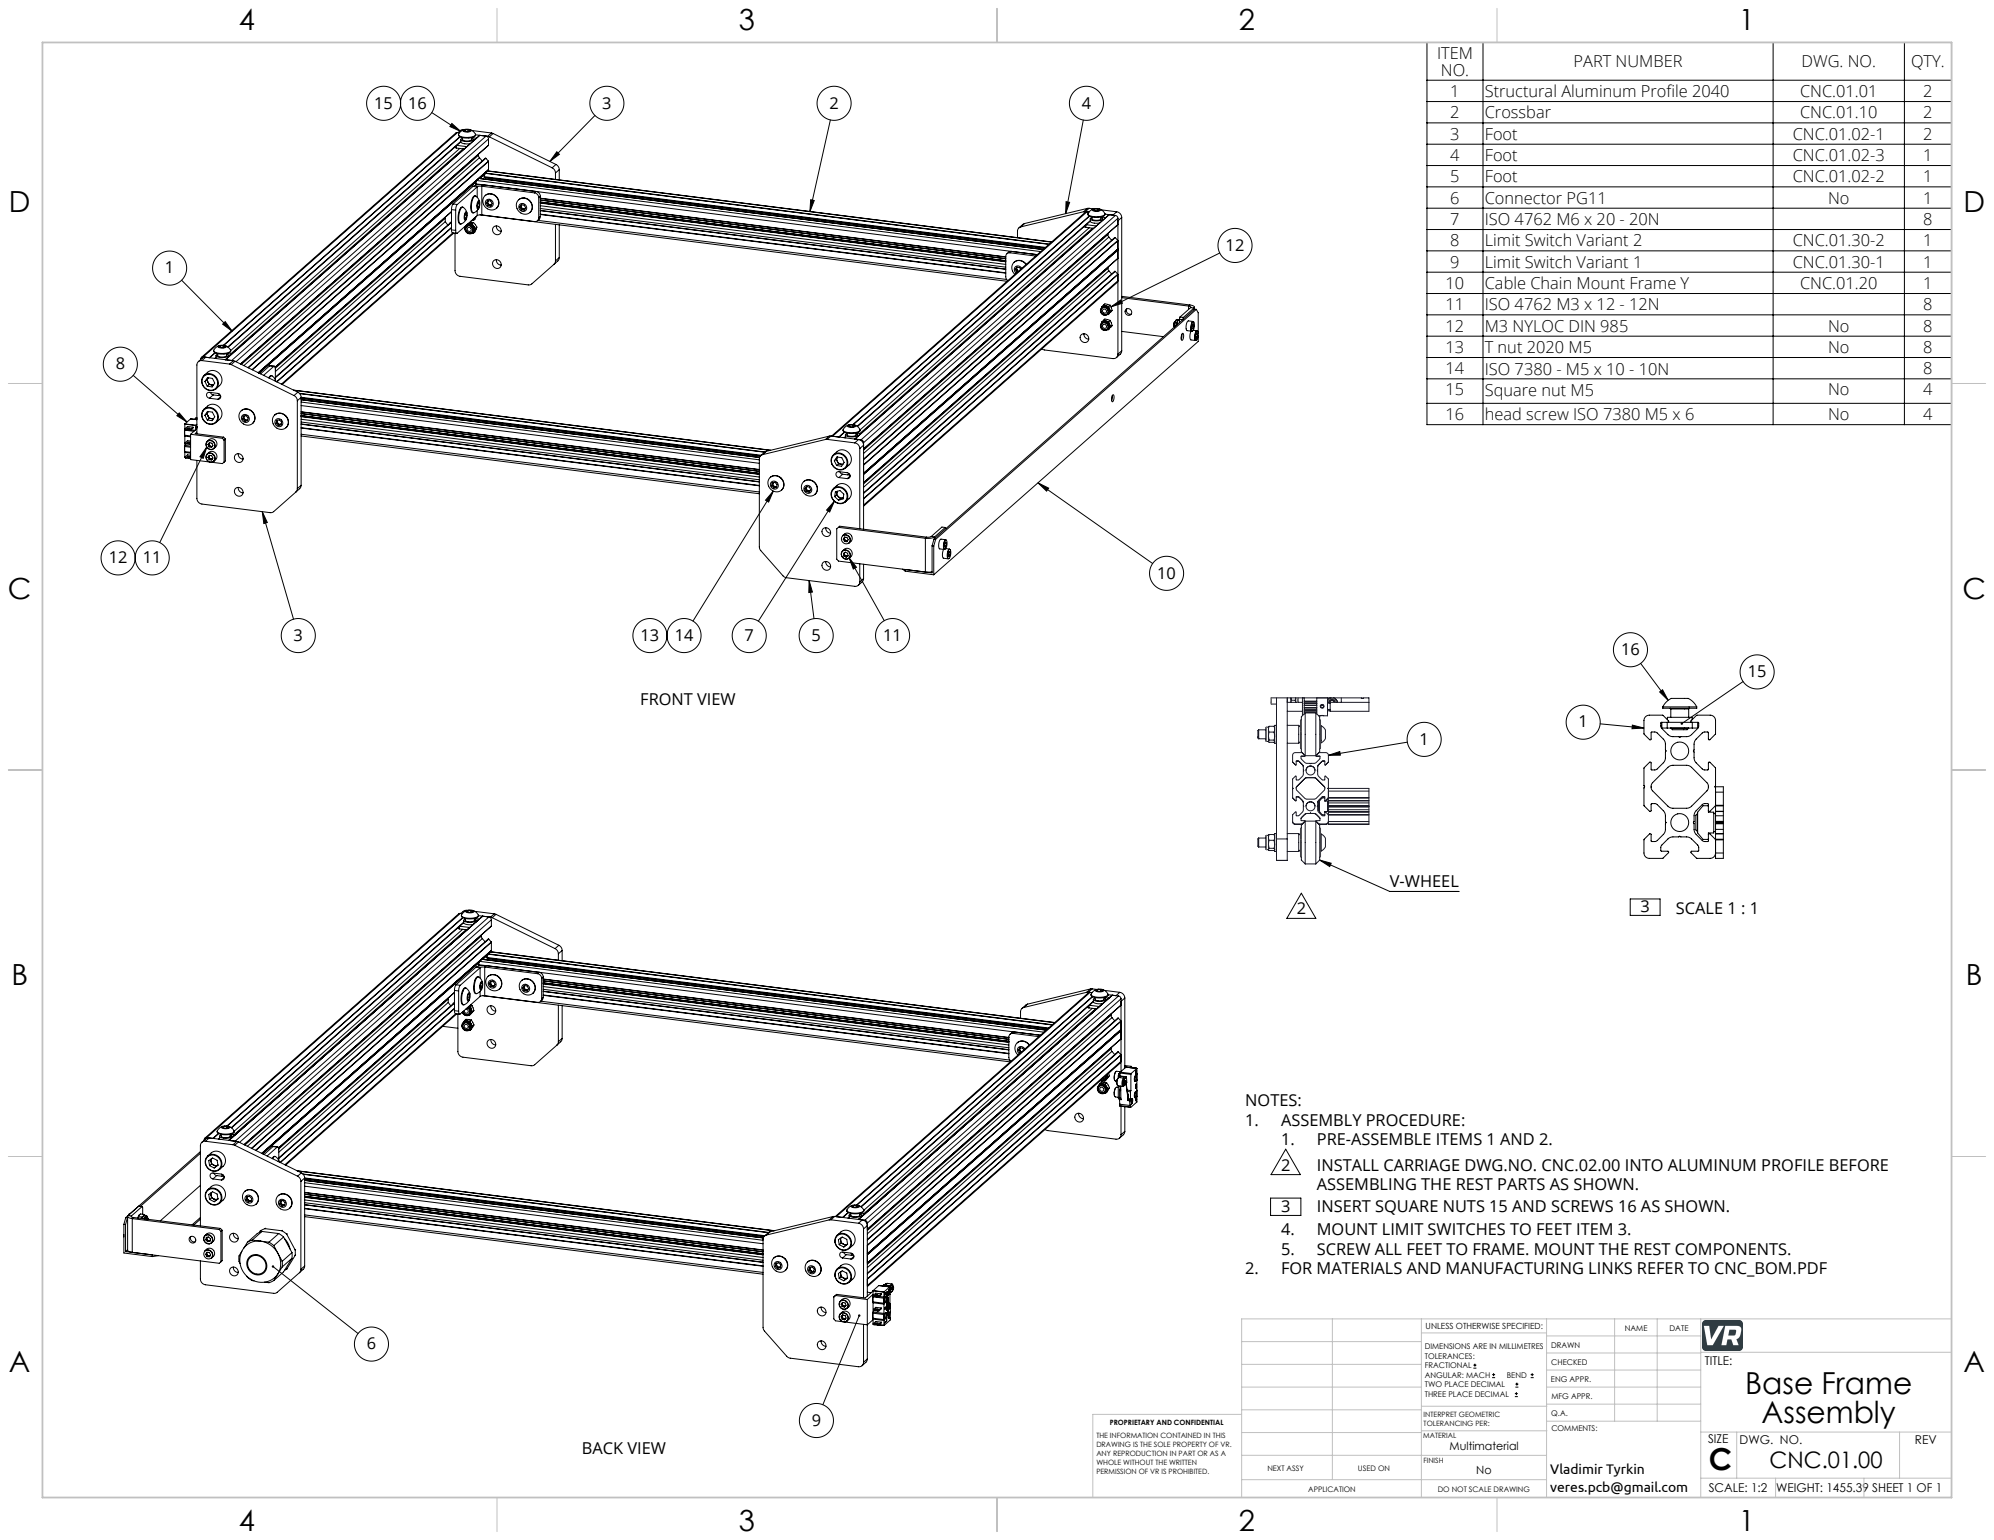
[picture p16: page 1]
FRONT VIEW; BACK VIEW; SCALE 1 : 1; INSTALL CARRIAGE DWG.NO. CNC.02.00 INTO ALUMINUM PROFILE BEFORE; INSERT SQUARE NUTS 15 AND SCREWS 16 AS SHOWN.; DWG. NO.; REV; Vladimir Tyrkin; CNC.01.00

ITEM NO. | PART NUMBER | DWG. NO. | QTY.
1 | Structural Aluminum Profile 2040 | CNC.01.01 | 2
2 | Crossbar | CNC.01.10 | 2
3 | Foot | CNC.01.02-1 | 2
4 | Foot | CNC.01.02-3 | 1
5 | Foot | CNC.01.02-2 | 1
6 | Connector PG11 | No | 1
7 | ISO 4762 M6 x 20 - 20N | | 8
8 | Limit Switch Variant 2 | CNC.01.30-2 | 1
9 | Limit Switch Variant 1 | CNC.01.30-1 | 1
10 | Cable Chain Mount Frame Y | CNC.01.20 | 1
11 | ISO 4762 M3 x 12 - 12N | | 8
12 | M3 NYLOC DIN 985 | No | 8
13 | T nut 2020 М5 | No | 8
14 | ISO 7380 - M5 x 10 - 10N | | 8
15 | Square nut M5 | No | 4
16 | head screw ISO 7380 M5 x 6 | No | 4

NOTES:
1. ASSEMBLY PROCEDURE:
1. PRE-ASSEMBLE ITEMS 1 AND 2.
ASSEMBLING THE REST PARTS AS SHOWN.
4. MOUNT LIMIT SWITCHES TO FEET ITEM 3.
5. SCREW ALL FEET TO FRAME. MOUNT THE REST COMPONENTS.
2. FOR MATERIALS AND MANUFACTURING LINKS REFER TO CNC_BOM.PDF

UNLESS OTHERWISE SPECIFIED: | | NAME | DATE
DIMENSIONS ARE IN MILLIMETRES TOLERANCES: FRACTIONAL ANGULAR: MACH BEND TWO PLACE DECIMAL THREE PLACE DECIMAL | DRAWN

CHECKED | | | TITLE: Base Frame Assembly

ENG APPR.
MFG APPR.

INTERPRET GEOMETRIC TOLERANCING PER: | Q.A.

PROPRIETARY AND CONFIDENTIAL
THE INFORMATION CONTAINED IN THIS
DRAWING IS THE SOLE PROPERTY OF VR.
ANY REPRODUCTION IN PART OR AS A
WHOLE WITHOUT THE WRITTEN
PERMISSION OF VR IS PROHIBITED.

NEXT ASSY | USED ON | No FINISH

APPLICATION | DO NOT SCALE DRAWING | | SCALE: 1:2 | WEIGHT: 1455.39 | SHEET 1 OF 1

veres.pcb@gmail.com

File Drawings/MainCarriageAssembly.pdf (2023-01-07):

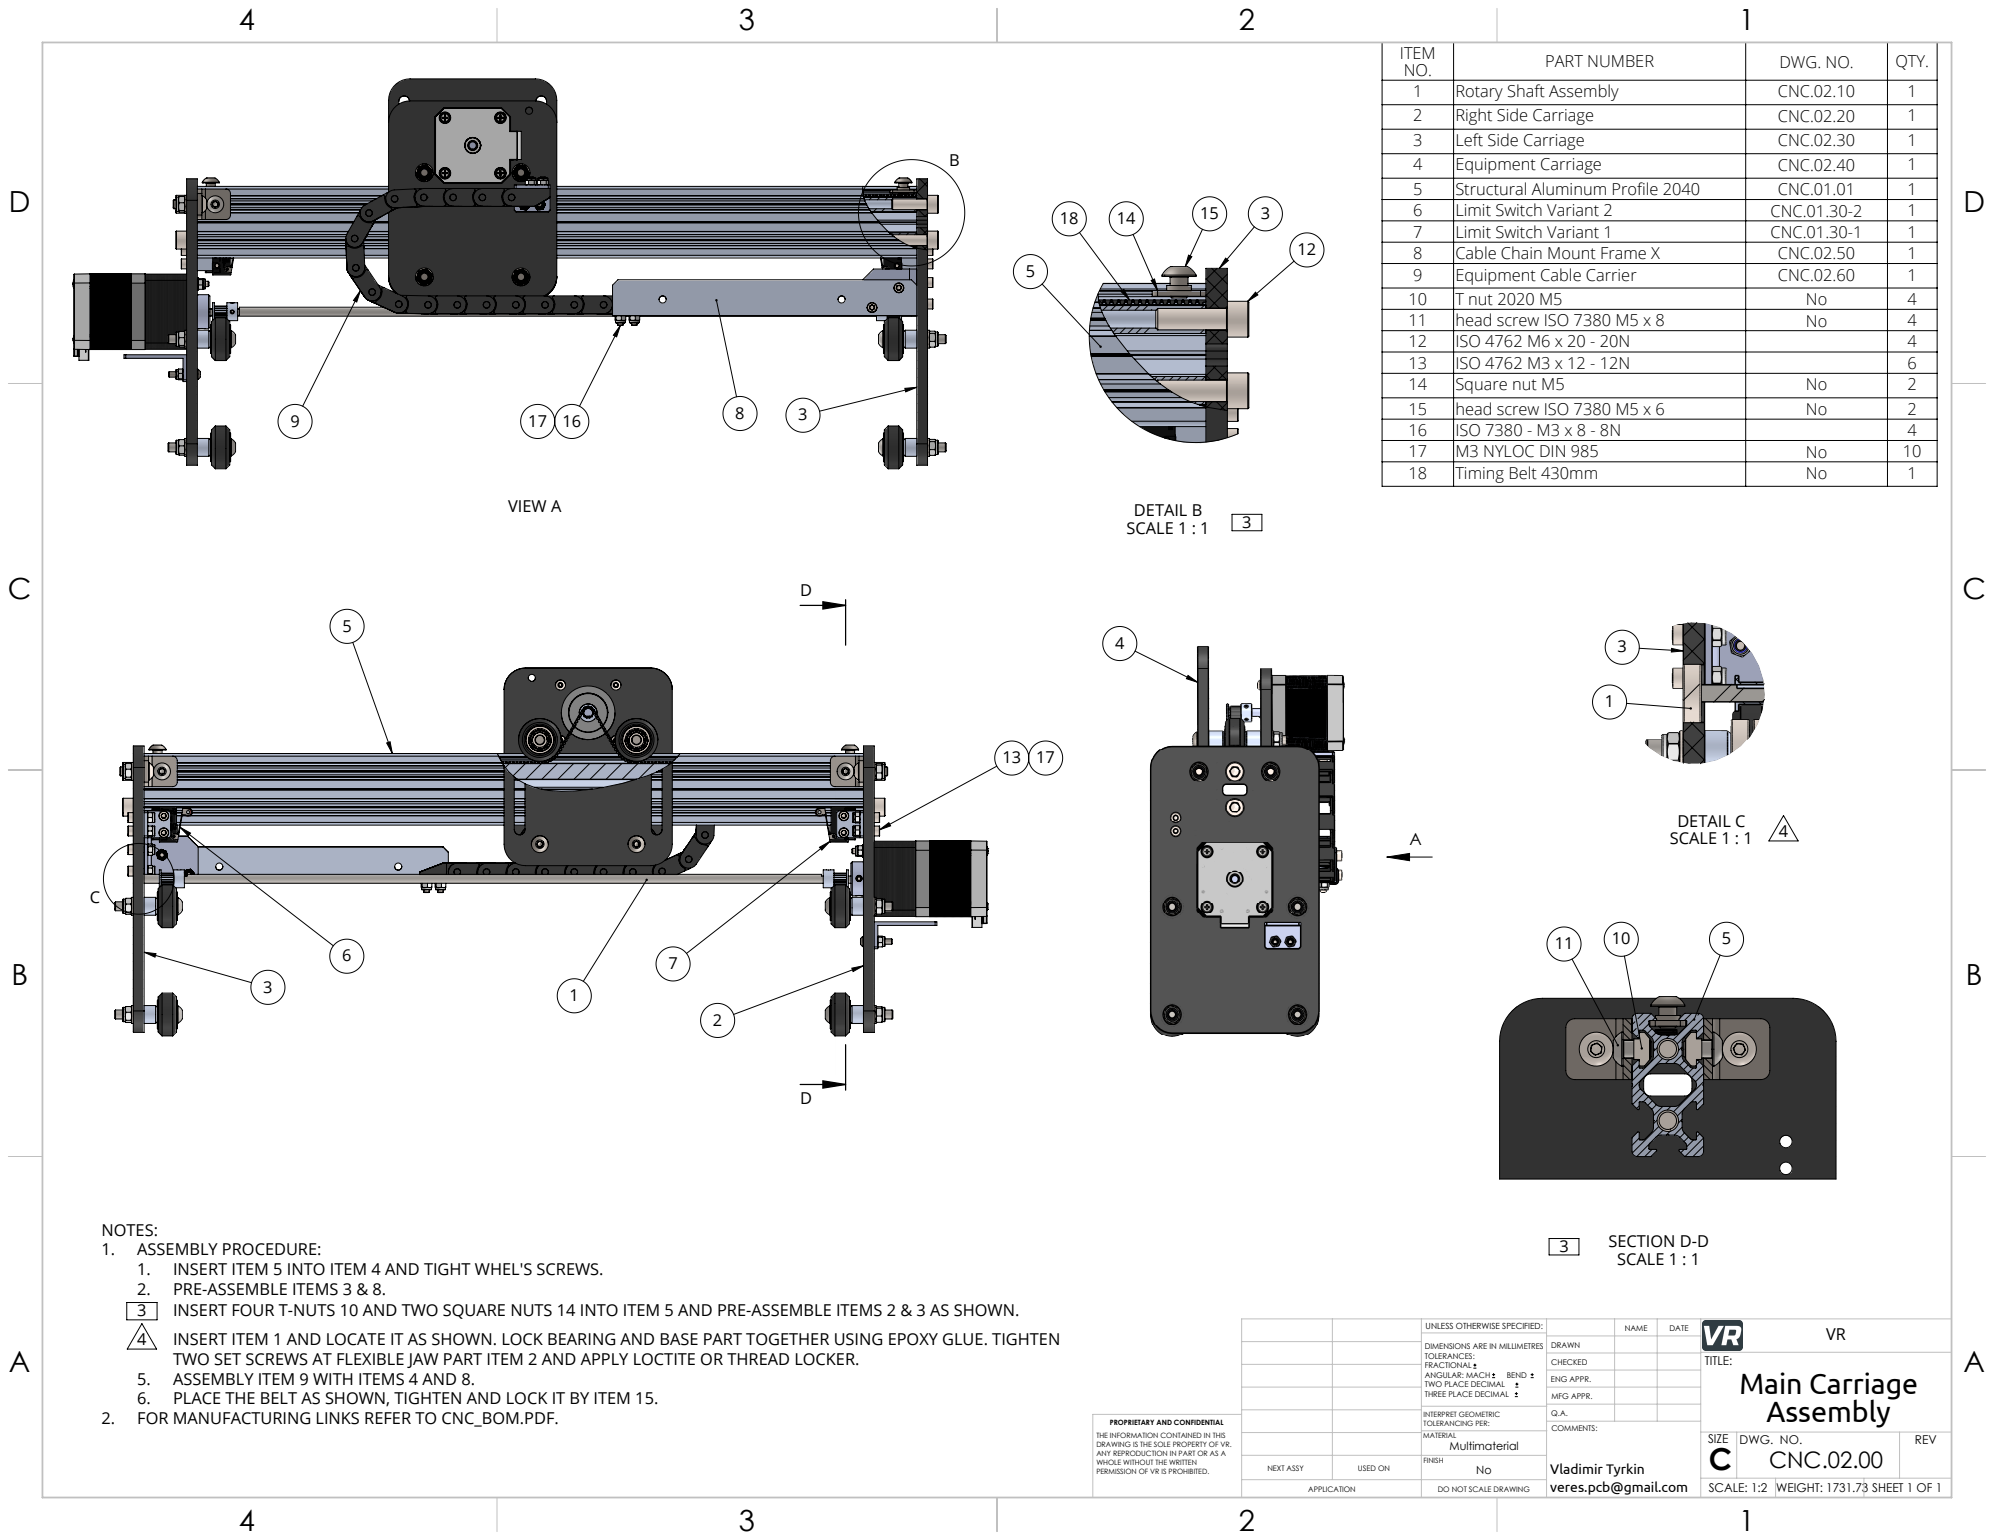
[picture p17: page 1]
VIEW A; DETAIL B SCALE 1 : 1; DETAIL C SCALE 1 : 1; SECTION D-D SCALE 1 : 1; INSERT FOUR T-NUTS 10 AND TWO SQUARE NUTS 14 INTO ITEM 5 AND PRE-ASSEMBLE ITEMS 2 & 3 AS SHOWN.; INSERT ITEM 1 AND LOCATE IT AS SHOWN. LOCK BEARING AND BASE PART TOGETHER USING EPOXY GLUE. TIGHTEN

ITEM NO. | PART NUMBER | DWG. NO. | QTY.
1 | Rotary Shaft Assembly | CNC.02.10 | 1
2 | Right Side Carriage | CNC.02.20 | 1
3 | Left Side Carriage | CNC.02.30 | 1
4 | Equipment Carriage | CNC.02.40 | 1
5 | Structural Aluminum Profile 2040 | CNC.01.01 | 1
6 | Limit Switch Variant 2 | CNC.01.30-2 | 1
7 | Limit Switch Variant 1 | CNC.01.30-1 | 1
8 | Cable Chain Mount Frame X | CNC.02.50 | 1
9 | Equipment Cable Carrier | CNC.02.60 | 1
10 | T nut 2020 М5 | No | 4
11 | head screw ISO 7380 M5 x 8 | No | 4
12 | ISO 4762 M6 x 20 - 20N | | 4
13 | ISO 4762 M3 x 12 - 12N | | 6
14 | Square nut M5 | No | 2
15 | head screw ISO 7380 M5 x 6 | No | 2
16 | ISO 7380 - M3 x 8 - 8N | | 4
17 | M3 NYLOC DIN 985 | No | 10
18 | Timing Belt 430mm | No | 1

NOTES:
1. ASSEMBLY PROCEDURE:
1. INSERT ITEM 5 INTO ITEM 4 AND TIGHT WHEL'S SCREWS.
2. PRE-ASSEMBLE ITEMS 3 & 8.
TWO SET SCREWS AT FLEXIBLE JAW PART ITEM 2 AND APPLY LOCTITE OR THREAD LOCKER.
5. ASSEMBLY ITEM 9 WITH ITEMS 4 AND 8.
6. PLACE THE BELT AS SHOWN, TIGHTEN AND LOCK IT BY ITEM 15.
2. FOR MANUFACTURING LINKS REFER TO CNC_BOM.PDF.

UNLESS OTHERWISE SPECIFIED: | | NAME | DATE | VR
DIMENSIONS ARE IN MILLIMETRES TOLERANCES: FRACTIONAL ANGULAR: MACH BEND TWO PLACE DECIMAL THREE PLACE DECIMAL | DRAWN

CHECKED | | | TITLE: Main Carriage Assembly

ENG APPR.
MFG APPR.

INTERPRET GEOMETRIC TOLERANCING PER: | Q.A.
MATERIAL Multimaterial | | SIZE C | DWG. NO. CNC.02.00 | REV

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

NEXT ASSY | USED ON | No FINISH

Vladimir Tyrkin
veres.pcb@gmail.com

APPLICATION | DO NOT SCALE DRAWING | | SCALE: 1:2 | WEIGHT: 1731.73 | SHEET 1 OF 1

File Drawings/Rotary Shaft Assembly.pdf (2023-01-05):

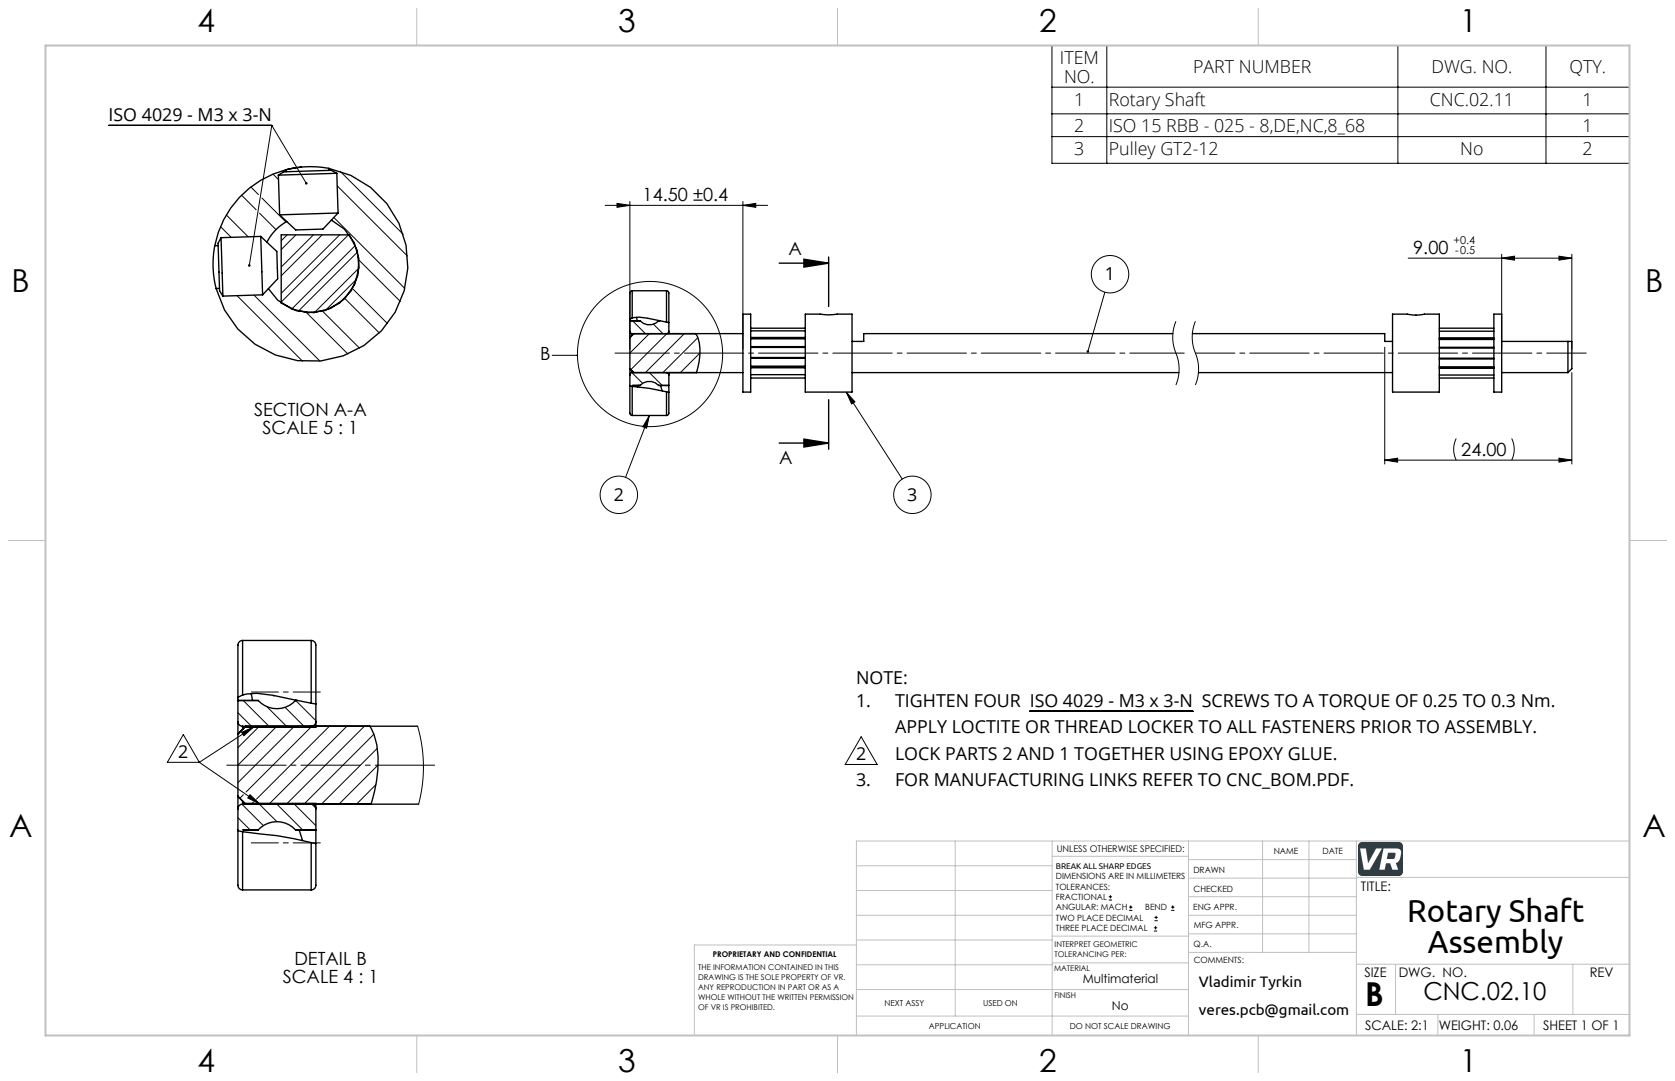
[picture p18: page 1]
SECTION A-A SCALE 5 : 1; ISO 4029 - M3 x 3-N; DETAIL B SCALE 4 : 1; LOCK PARTS 2 AND 1 TOGETHER USING EPOXY GLUE.; OF VR IS PROHIBITED.; veres.pcb@gmail.com; Vladimir Tyrkin

ITEM NO. | PART NUMBER | DWG. NO. | QTY.
1 | Rotary Shaft | CNC.02.11 | 1
2 | ISO 15 RBB - 025 - 8,DE,NC,8_68 | | 1
3 | Pulley GT2-12 | No | 2

NOTE:
1. TIGHTEN FOUR ISO 4029 - M3 x 3-N SCREWS TO A TORQUE OF 0.25 TO 0.3 Nm.
APPLY LOCTITE OR THREAD LOCKER TO ALL FASTENERS PRIOR TO ASSEMBLY.
3. FOR MANUFACTURING LINKS REFER TO CNC_BOM.PDF.

UNLESS OTHERWISE SPECIFIED: | | NAME | DATE
BREAK ALL SHARP EDGES DIMENSIONS ARE IN MILLIMETERS TOLERANCES: FRACTIONAL ANGULAR: MACH BEND TWO PLACE DECIMAL THREE PLACE DECIMAL | DRAWN

CHECKED | | | TITLE: Rotary Shaft Assembly

ENG APPR.
MFG APPR.

INTERPRET GEOMETRIC TOLERANCING PER: | Q.A.
MATERIAL Multimaterial | | SIZE B | DWG. NO. CNC.02.10 | REV

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

NEXT ASSY | USED ON | No FINISH

APPLICATION | DO NOT SCALE DRAWING | | SCALE: 2:1 | WEIGHT: 0.06 | SHEET 1 OF 1

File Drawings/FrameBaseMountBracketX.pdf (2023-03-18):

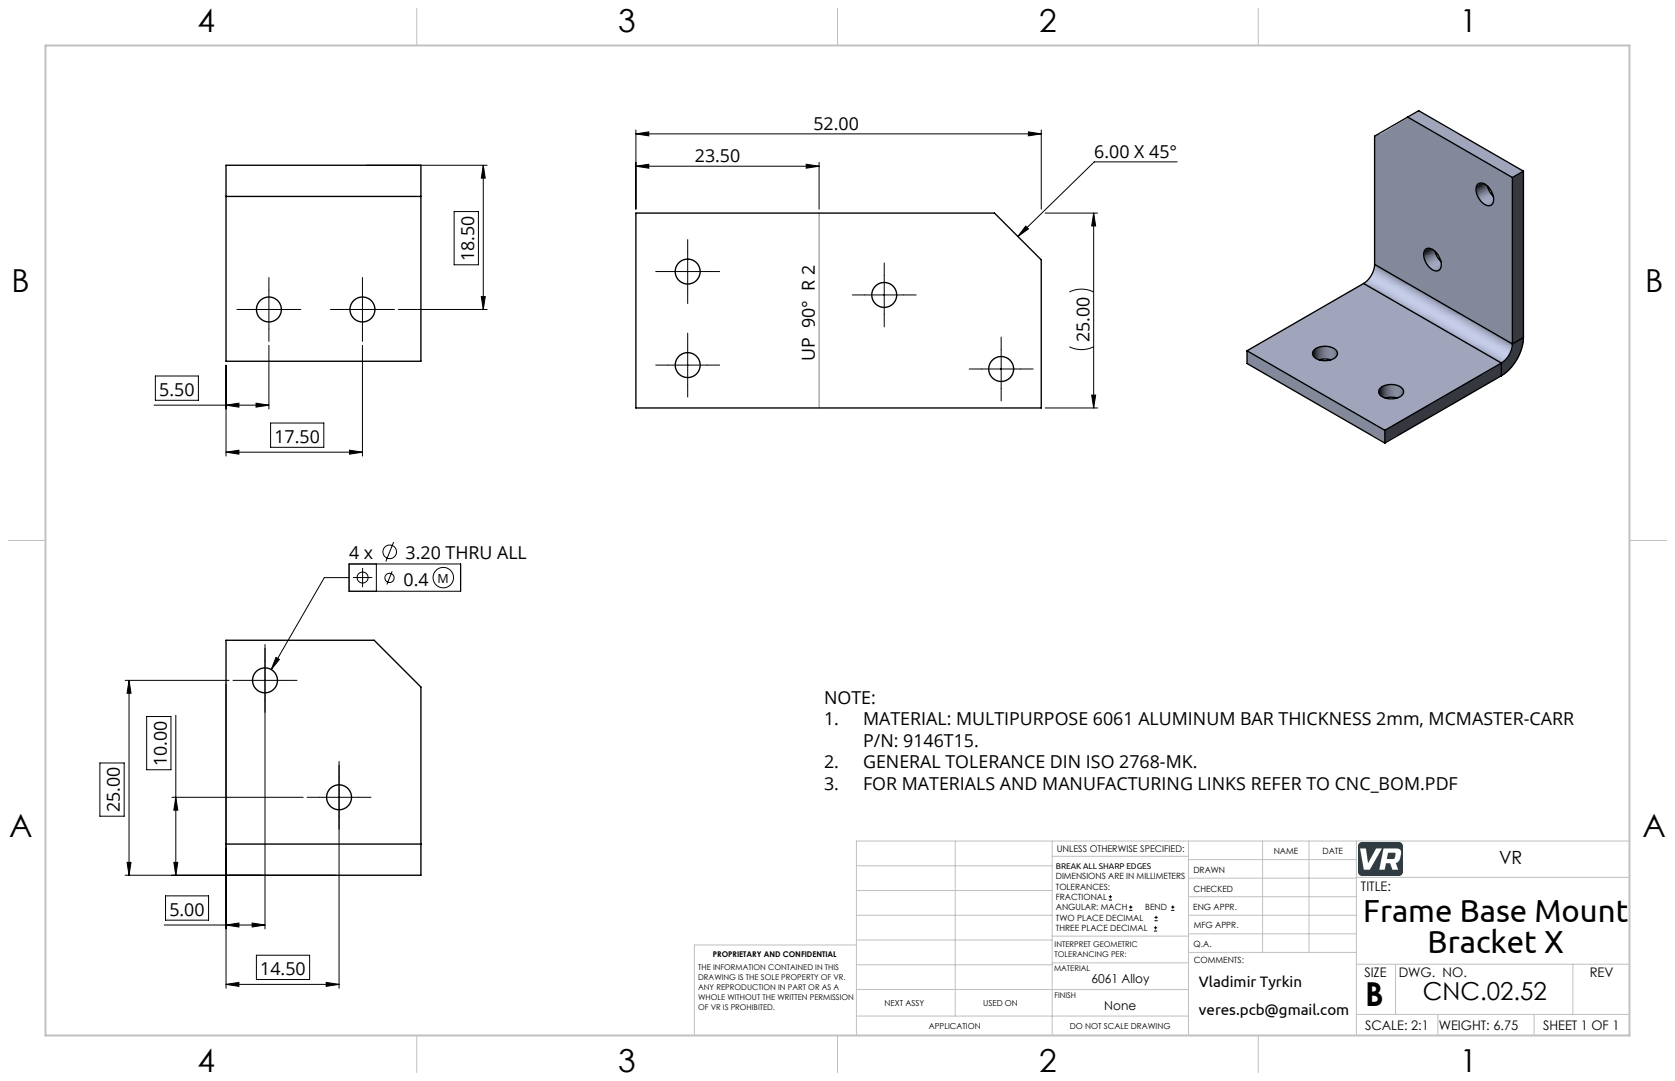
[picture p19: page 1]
3.20 THRU ALL; ENG APPR.; OF VR IS PROHIBITED.; veres.pcb@gmail.com; Vladimir Tyrkin

NOTE:
1. MATERIAL: MULTIPURPOSE 6061 ALUMINUM BAR THICKNESS 2mm, MCMASTER-CARR
2. GENERAL TOLERANCE DIN ISO 2768-MK.
3. FOR MATERIALS AND MANUFACTURING LINKS REFER TO CNC_BOM.PDF

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

CHECKED | | TITLE: Frame Base Mount Bracket X

MFG APPR.

INTERPRET GEOMETRIC TOLERANCING PER: | Q.A.
MATERIAL 6061 Alloy | | SIZE B | DWG. NO. CNC.02.52 | REV

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

NEXT ASSY | USED ON | None FINISH

APPLICATION | DO NOT SCALE DRAWING | | SCALE: 2:1 | WEIGHT: 6.75 | SHEET 1 OF 1

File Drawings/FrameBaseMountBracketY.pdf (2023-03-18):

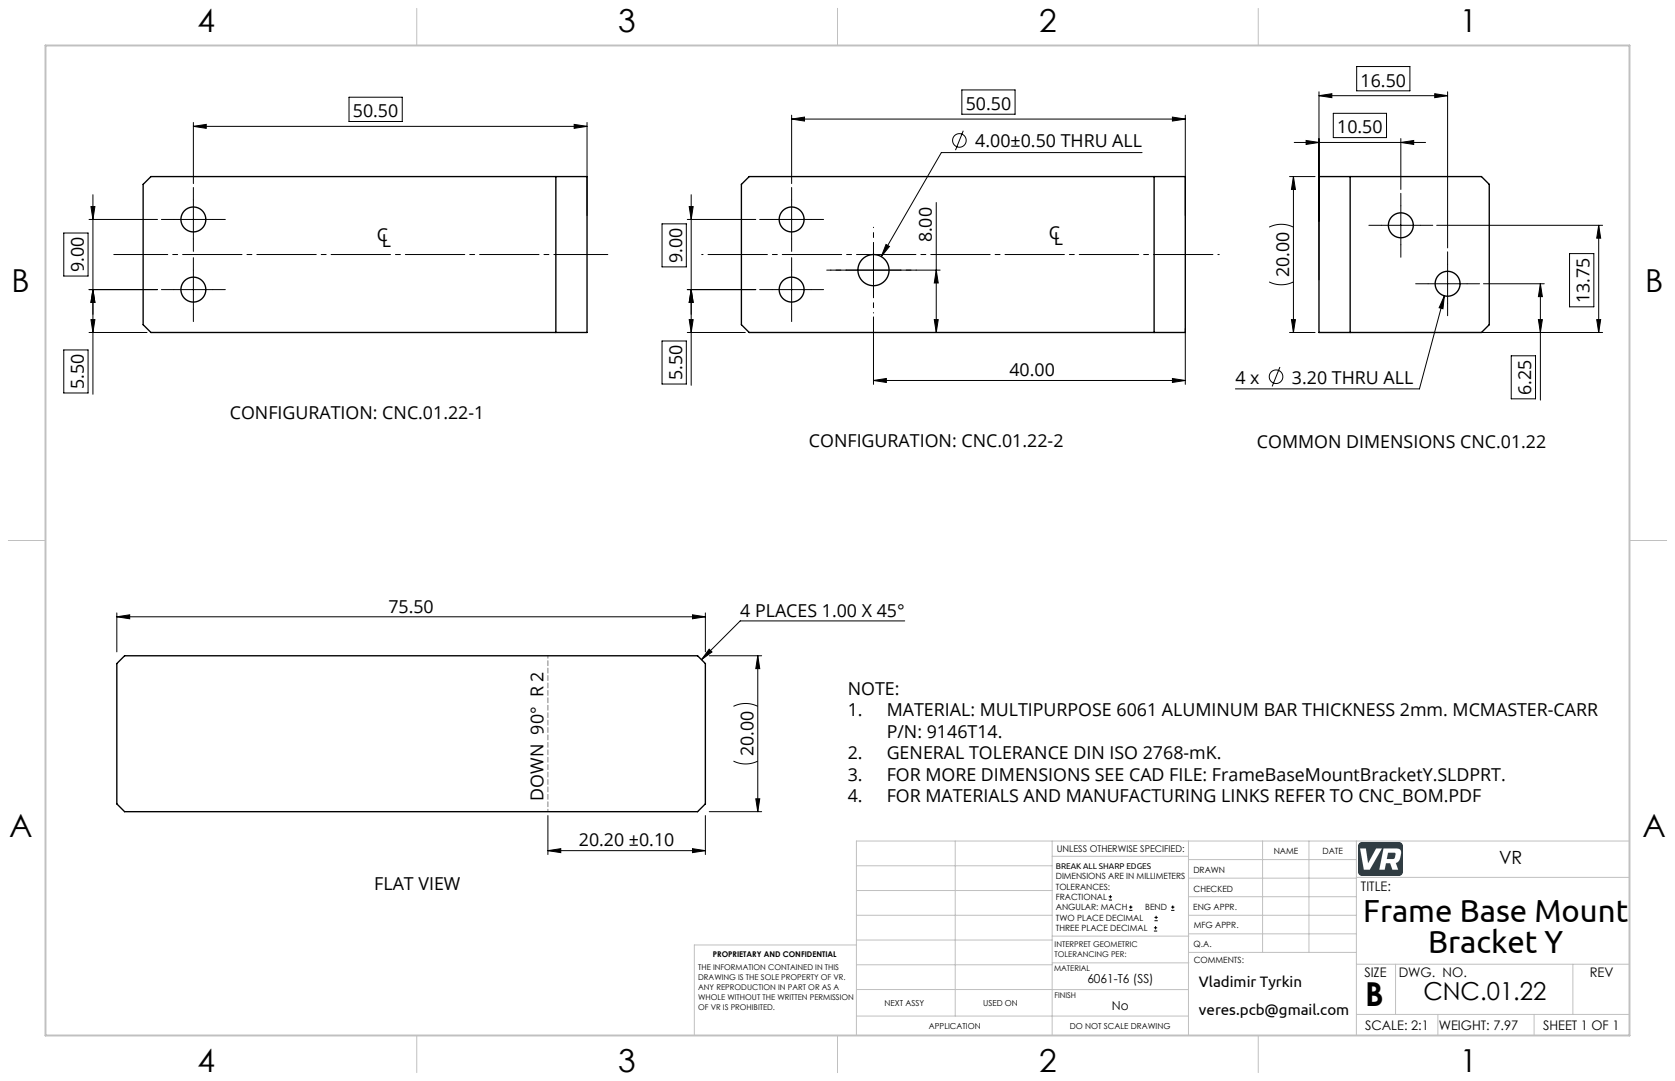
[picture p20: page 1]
CONFIGURATION: CNC.01.22-1; 4.00±0.50 THRU ALL; CONFIGURATION: CNC.01.22-2; 3.20 THRU ALL; 4 PLACES 1.00 X 45°; DOWN 90° R 2; FLAT VIEW; OF VR IS PROHIBITED.; veres.pcb@gmail.com; Vladimir Tyrkin

COMMON DIMENSIONS CNC.01.22

NOTE:
1. MATERIAL: MULTIPURPOSE 6061 ALUMINUM BAR THICKNESS 2mm. MCMASTER-CARR
2. GENERAL TOLERANCE DIN ISO 2768-mK.
3. FOR MORE DIMENSIONS SEE CAD FILE: FrameBaseMountBracketY.SLDPRT.
4. FOR MATERIALS AND MANUFACTURING LINKS REFER TO CNC_BOM.PDF

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

CHECKED | | TITLE: Frame Base Mount Bracket Y

ENG APPR.
MFG APPR.

INTERPRET GEOMETRIC TOLERANCING PER: | Q.A.
MATERIAL 6061-T6 (SS) | | SIZE B | DWG. NO. CNC.01.22 | REV

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

NEXT ASSY | USED ON | No FINISH

APPLICATION | DO NOT SCALE DRAWING | | SCALE: 2:1 | WEIGHT: 7.97 | SHEET 1 OF 1

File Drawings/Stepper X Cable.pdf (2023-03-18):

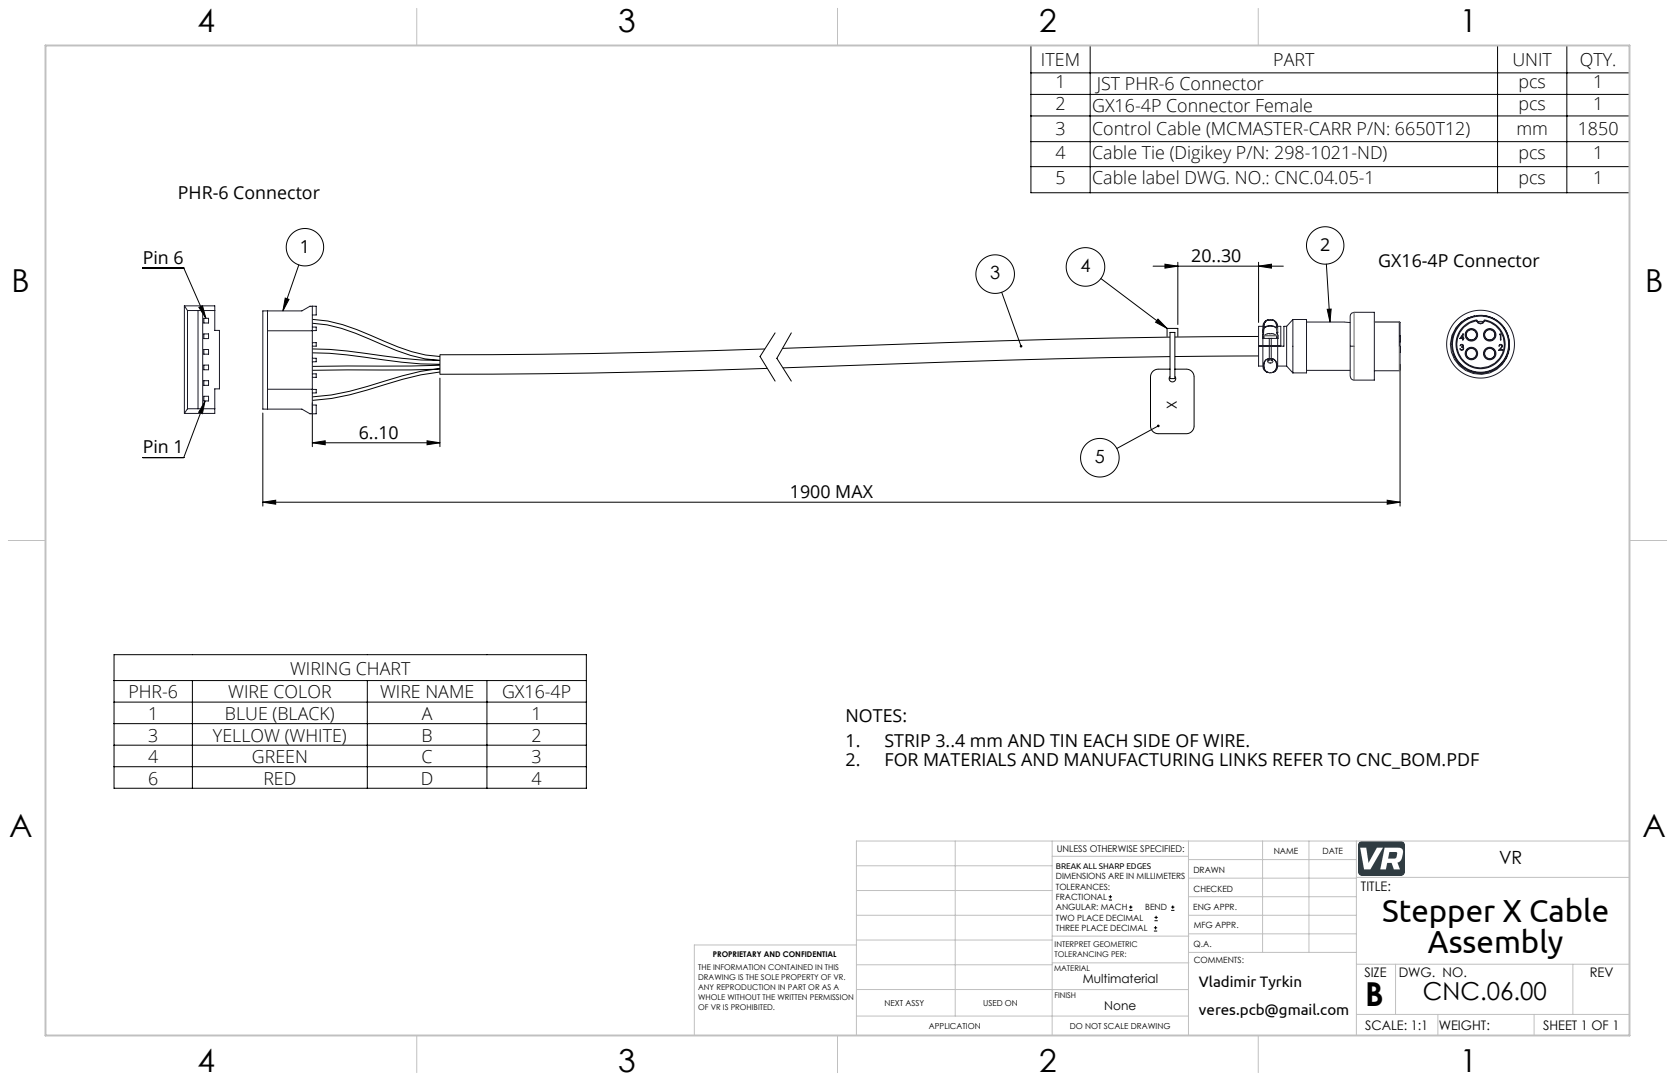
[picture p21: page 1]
1900 MAX; Pin 1; Pin 6; PHR-6 Connector; GX16-4P Connector; WIRING CHART; OF VR IS PROHIBITED.; veres.pcb@gmail.com; Vladimir Tyrkin

ITEM | PART | UNIT | QTY.
1 | JST PHR-6 Connector | pcs | 1
2 | GX16-4P Connector Female | pcs | 1
3 | Control Cable (MCMASTER-CARR P/N: 6650T12) | mm | 1850
4 | Cable Tie (Digikey P/N: 298-1021-ND) | pcs | 1
5 | Cable label DWG. NO.: CNC.04.05-1 | pcs | 1

PHR-6 | WIRE COLOR | WIRE NAME | GX16-4P
1 | BLUE (BLACK) | A | 1
3 | YELLOW (WHITE) | B | 2
4 | GREEN | C | 3
6 | RED | D | 4

NOTES:
1. STRIP 3..4 mm AND TIN EACH SIDE OF WIRE.
2. FOR MATERIALS AND MANUFACTURING LINKS REFER TO CNC_BOM.PDF

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

CHECKED | | TITLE: Stepper X Cable Assembly

ENG APPR.
MFG APPR.

INTERPRET GEOMETRIC TOLERANCING PER: | Q.A.
MATERIAL Multimaterial | | SIZE B | DWG. NO. CNC.06.00 | REV

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

NEXT ASSY | USED ON | None FINISH

APPLICATION | DO NOT SCALE DRAWING | | SCALE: 1:1 | WEIGHT: | SHEET 1 OF 1

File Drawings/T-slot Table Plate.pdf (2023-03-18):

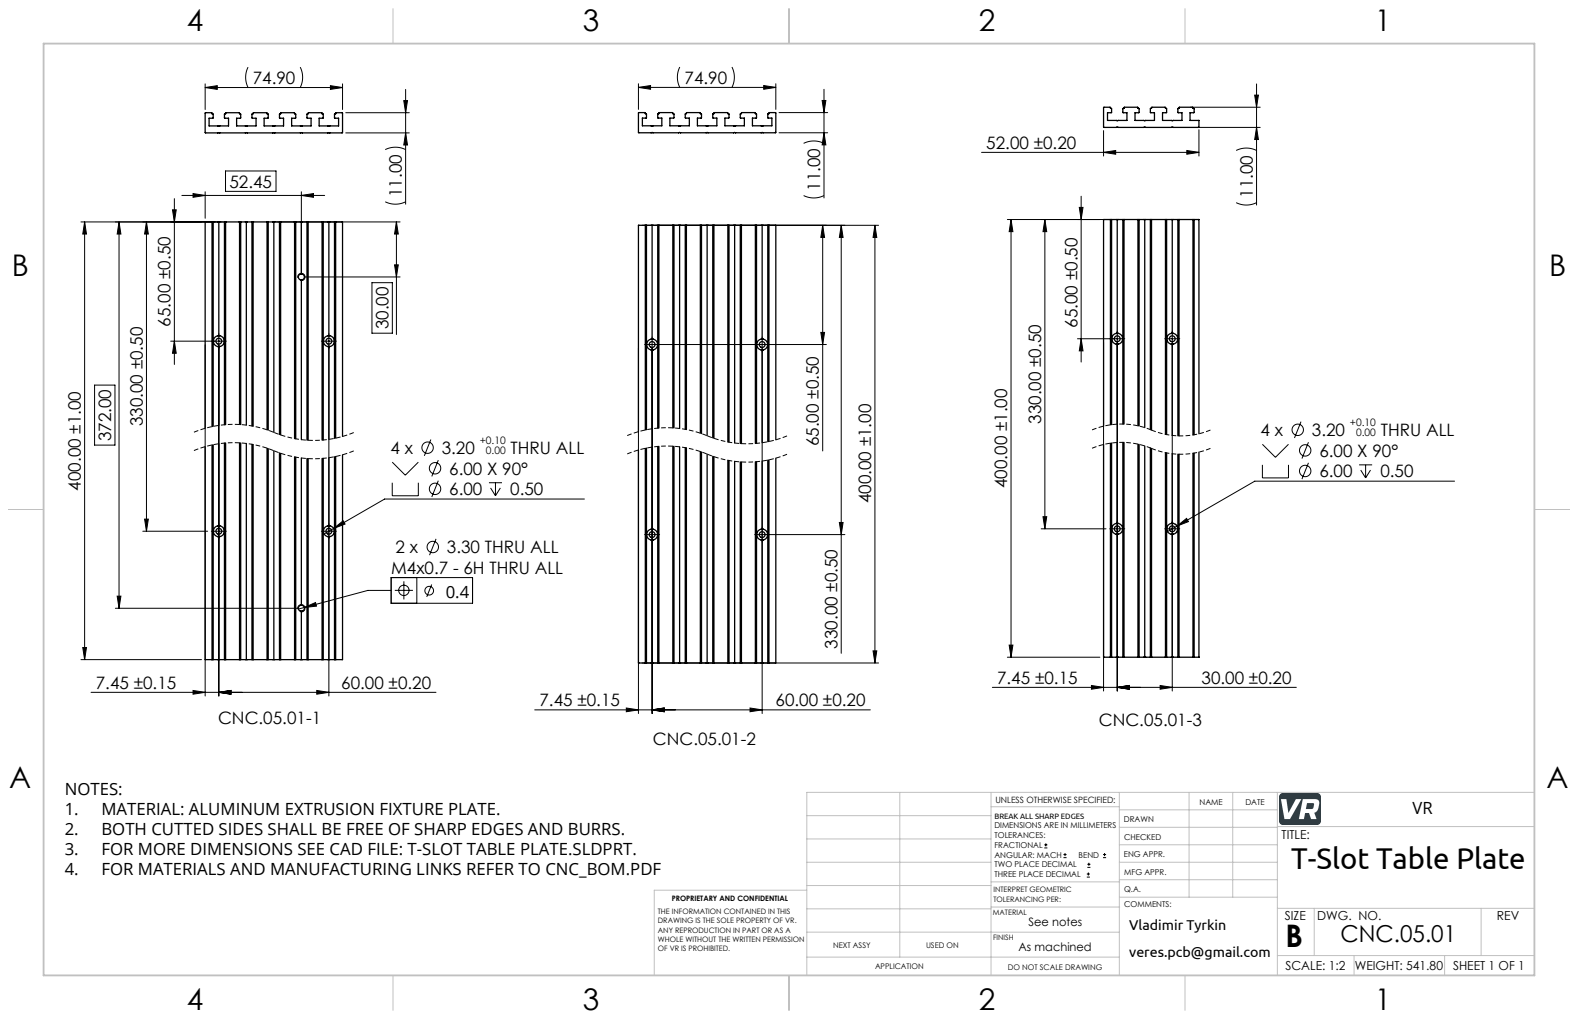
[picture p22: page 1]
0.00 THRU ALL 6.00 X 90° 6.00 0.50; 3.30 THRU ALL; M4x0.7 - 6H THRU ALL; 0.00 THRU ALL 6.00 X 90°; OF VR IS PROHIBITED.; veres.pcb@gmail.com; Vladimir Tyrkin

NOTES:
1. MATERIAL: ALUMINUM EXTRUSION FIXTURE PLATE.
2. BOTH CUTTED SIDES SHALL BE FREE OF SHARP EDGES AND BURRS.
3. FOR MORE DIMENSIONS SEE CAD FILE: T-SLOT TABLE PLATE.SLDPRT.
4. FOR MATERIALS AND MANUFACTURING LINKS REFER TO CNC_BOM.PDF

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

CHECKED | | TITLE: T-Slot Table Plate

ENG APPR.
MFG APPR.

INTERPRET GEOMETRIC TOLERANCING PER: | Q.A.
MATERIAL See notes | | SIZE B | DWG. NO. CNC.05.01 | REV

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

NEXT ASSY | USED ON | As machined FINISH

APPLICATION | DO NOT SCALE DRAWING | | SCALE: 1:2 | WEIGHT: 541.80 | SHEET 1 OF 1

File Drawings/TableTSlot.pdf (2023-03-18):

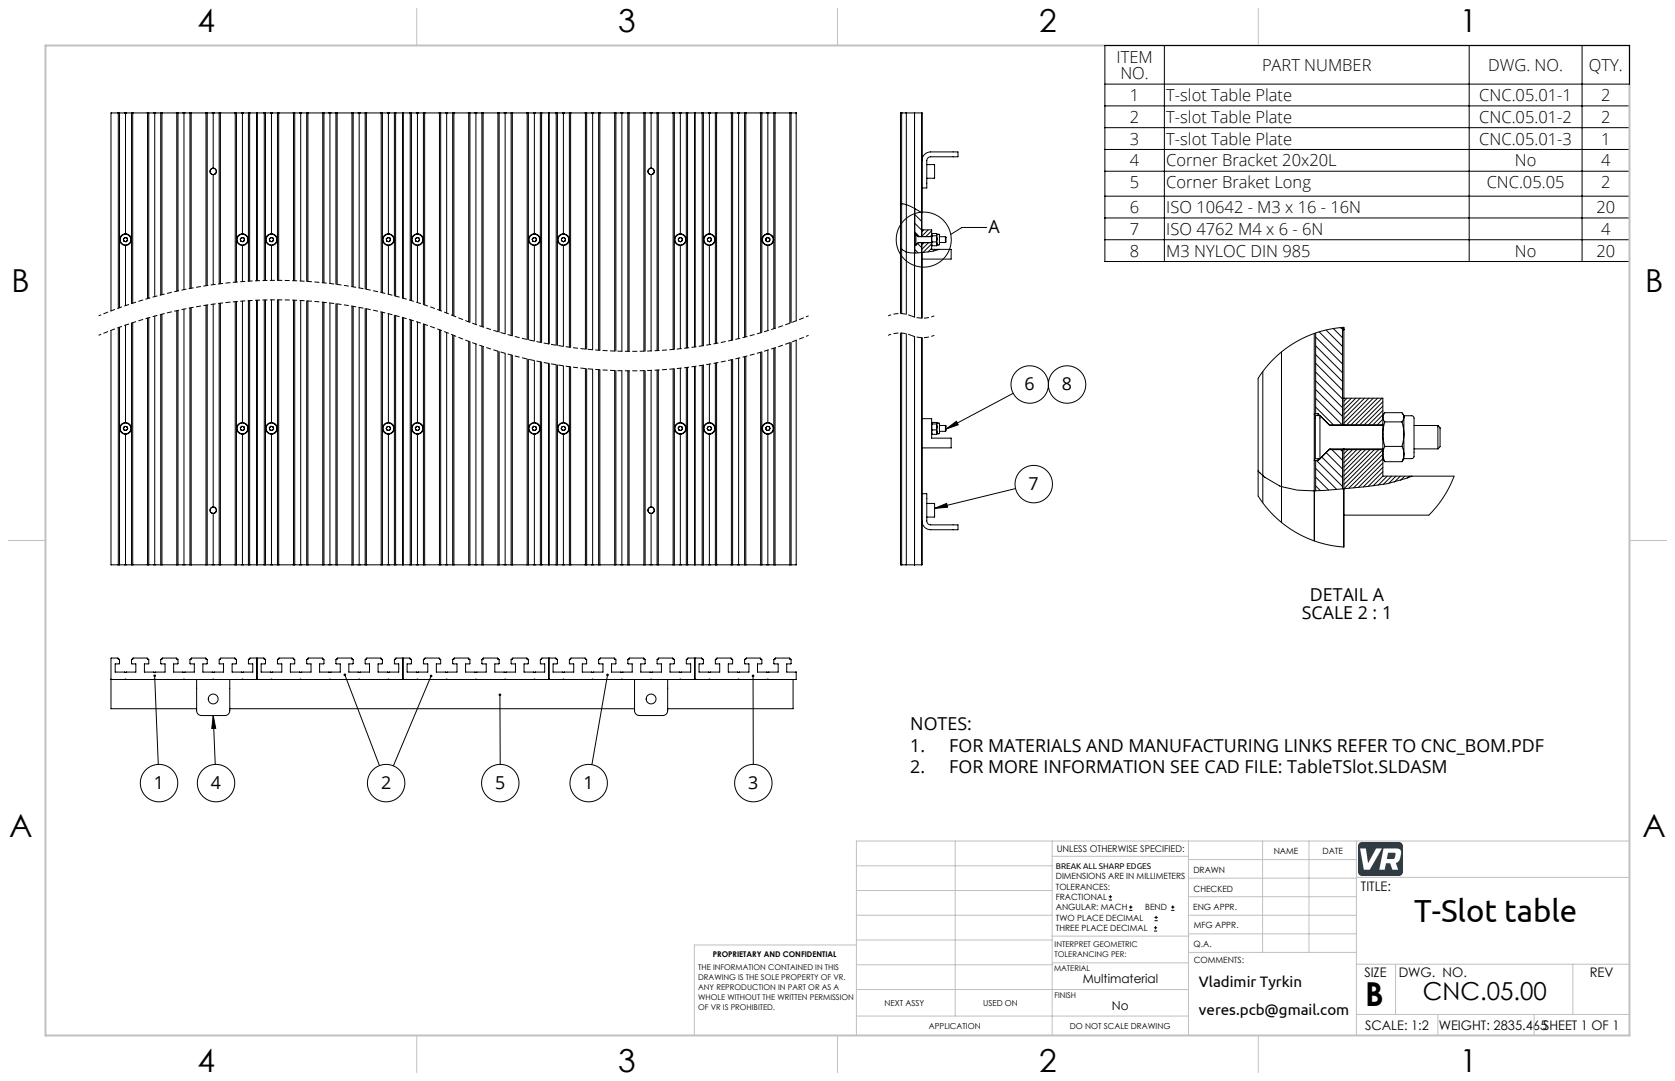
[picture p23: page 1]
DETAIL A SCALE 2 : 1; OF VR IS PROHIBITED.; veres.pcb@gmail.com; Vladimir Tyrkin

ITEM NO. | PART NUMBER | DWG. NO. | QTY.
1 | T-slot Table Plate | CNC.05.01-1 | 2
2 | T-slot Table Plate | CNC.05.01-2 | 2
3 | T-slot Table Plate | CNC.05.01-3 | 1
4 | Corner Bracket 20х20L | No | 4
5 | Corner Braket Long | CNC.05.05 | 2
6 | ISO 10642 - M3 x 16 - 16N | | 20
7 | ISO 4762 M4 x 6 - 6N | | 4
8 | M3 NYLOC DIN 985 | No | 20

NOTES:
1. FOR MATERIALS AND MANUFACTURING LINKS REFER TO CNC_BOM.PDF
2. FOR MORE INFORMATION SEE CAD FILE: TableTSlot.SLDASM

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

CHECKED | | | TITLE: T-Slot table

ENG APPR.
MFG APPR.

INTERPRET GEOMETRIC TOLERANCING PER: | Q.A.
MATERIAL Multimaterial | | SIZE B | DWG. NO. CNC.05.00 | REV

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

NEXT ASSY | USED ON | No FINISH

APPLICATION | DO NOT SCALE DRAWING | | SCALE: 1:2 | WEIGHT: 2835.465 | SHEET 1 OF 1

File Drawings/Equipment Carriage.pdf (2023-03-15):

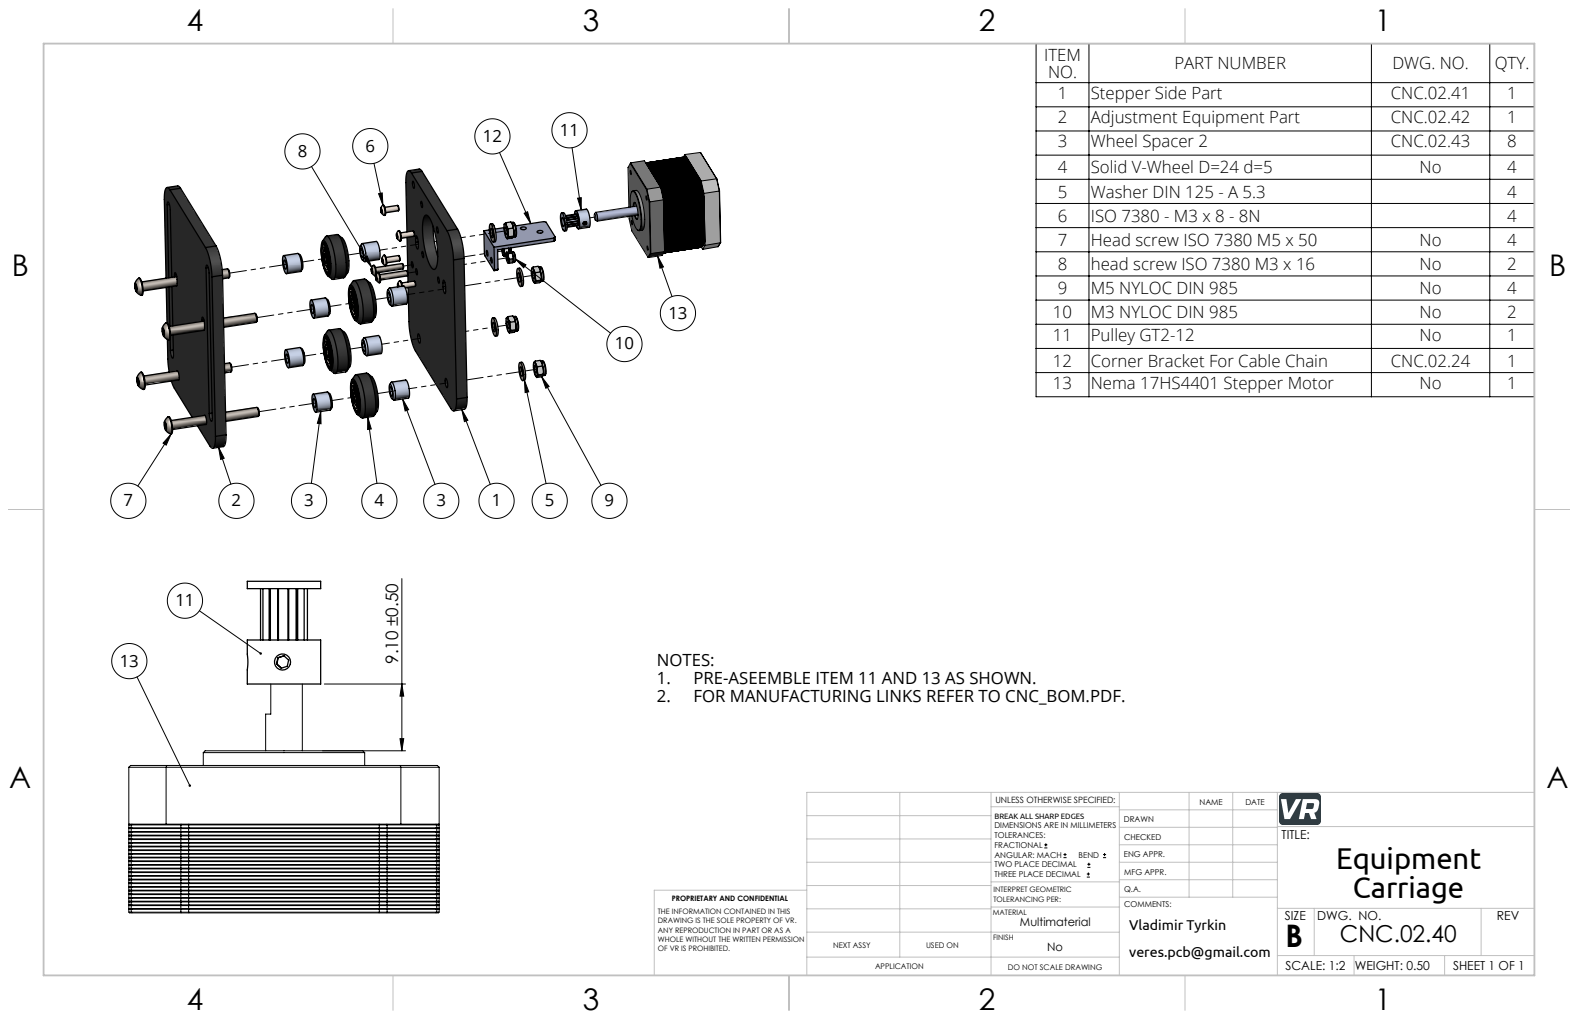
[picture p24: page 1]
OF VR IS PROHIBITED.; veres.pcb@gmail.com; Vladimir Tyrkin

ITEM NO. | PART NUMBER | DWG. NO. | QTY.
1 | Stepper Side Part | CNC.02.41 | 1
2 | Adjustment Equipment Part | CNC.02.42 | 1
3 | Wheel Spacer 2 | CNC.02.43 | 8
4 | Solid V-Wheel D=24 d=5 | No | 4
5 | Washer DIN 125 - A 5.3 | | 4
6 | ISO 7380 - M3 x 8 - 8N | | 4
7 | Head screw ISO 7380 M5 x 50 | No | 4
8 | head screw ISO 7380 M3 x 16 | No | 2
9 | M5 NYLOC DIN 985 | No | 4
10 | M3 NYLOC DIN 985 | No | 2
11 | Pulley GT2-12 | No | 1
12 | Corner Bracket For Cable Chain | CNC.02.24 | 1
13 | Nema 17HS4401 Stepper Motor | No | 1

1. PRE-ASEEMBLE ITEM 11 AND 13 AS SHOWN.
2. FOR MANUFACTURING LINKS REFER TO CNC_BOM.PDF.

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

CHECKED | | | TITLE: Equipment Carriage

ENG APPR.
MFG APPR.

INTERPRET GEOMETRIC TOLERANCING PER: | Q.A.
MATERIAL Multimaterial | | SIZE B | DWG. NO. CNC.02.40 | REV

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

NEXT ASSY | USED ON | No FINISH

APPLICATION | DO NOT SCALE DRAWING | | SCALE: 1:2 | WEIGHT: 0.50 | SHEET 1 OF 1

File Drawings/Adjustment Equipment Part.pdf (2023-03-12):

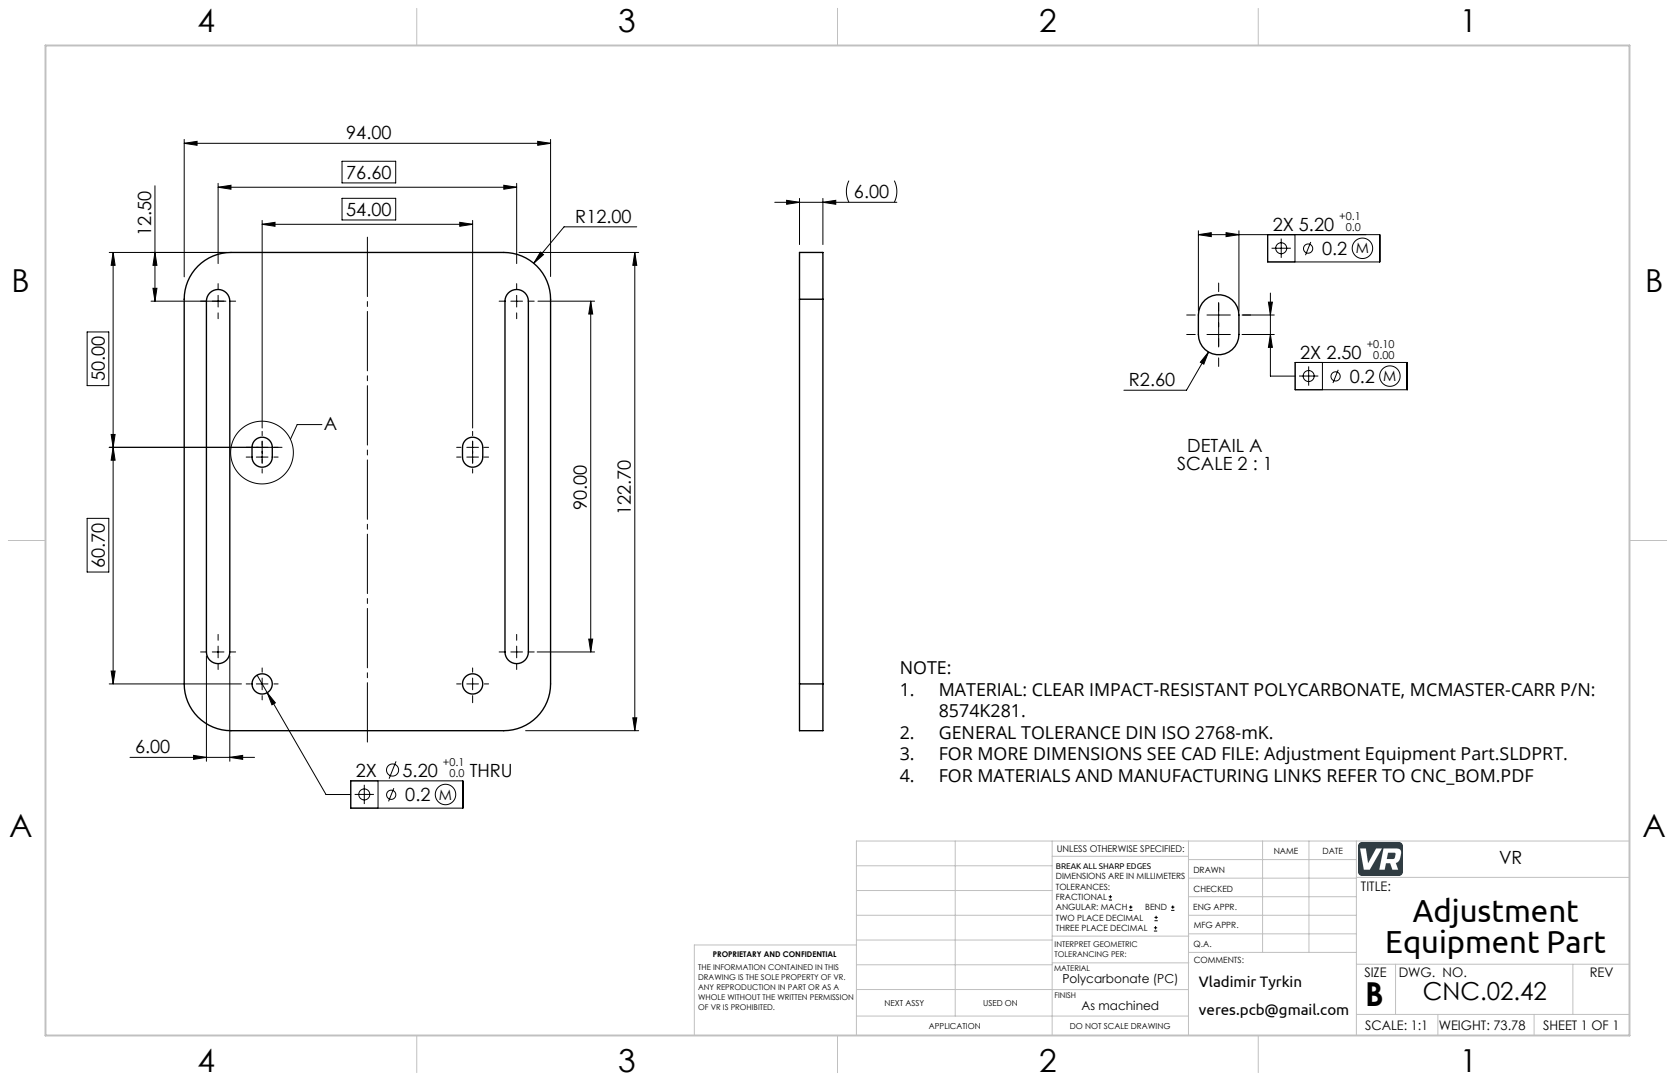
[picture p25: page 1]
2Х 5.20 +0.1 0.0 THRU 0.2 M; DETAIL A SCALE 2 : 1; OF VR IS PROHIBITED.; veres.pcb@gmail.com; Vladimir Tyrkin

NOTE:
1. MATERIAL: CLEAR IMPACT-RESISTANT POLYCARBONATE, MCMASTER-CARR P/N:
2. GENERAL TOLERANCE DIN ISO 2768-mK.
3. FOR MORE DIMENSIONS SEE CAD FILE: Adjustment Equipment Part.SLDPRT.
4. FOR MATERIALS AND MANUFACTURING LINKS REFER TO CNC_BOM.PDF

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

CHECKED | | TITLE: Adjustment Equipment Part

ENG APPR.
MFG APPR.

INTERPRET GEOMETRIC TOLERANCING PER: | Q.A.
MATERIAL Polycarbonate (PC) | | SIZE B | DWG. NO. CNC.02.42 | REV

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

NEXT ASSY | USED ON | As machined FINISH

APPLICATION | DO NOT SCALE DRAWING | | SCALE: 1:1 | WEIGHT: 73.78 | SHEET 1 OF 1

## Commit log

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2020-12-30 Make some files non virtual
    [Assem vacuum table.SLDASM, AssemblyCorner.SLDASM, BaseFrameAssembly.SLDASM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]
2020-12-30 Make some files virtual
    [CableChainForXCarriage.SLDASM, CableChainForYCarriage.SLDASM, LaserCarriage.SLDASM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]
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2021-01-05 Some changes with cables, and add milling carriage just for reference
    [BaseFrameAssembly.SLDASM, CableChainForXCarriage.SLDASM, CableChainForYCarriage.SLDASM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]
2021-01-05 Add table with T-slots
    [CableChainForXCarriage.SLDASM, CableChainForYCarriage.SLDASM, LeftSideCarriage.SLDASM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]
2021-01-07 Update T slot table & Milling carriage
    [BaseFrameAssembly.SLDASM, CableChainForXCarriage.SLDASM, CableChainForYCarriage.SLDASM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]
2021-01-09 Added holes for joint T slot table between each other
    [BaseFrameAssembly.SLDASM, CableChainForYCarriage.SLDASM, LeftSideCarriage.SLDASM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]
2021-01-09 Almost done T slot table
    [BaseFrameAssembly.SLDASM, CableChainForYCarriage.SLDASM, FootMount.SLDASM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]
2021-01-29 Almost done electrical scheme
    [AnotherCarriageZ.SLDPRT, BaseFrameAssembly.SLDASM, CableChainForXCarriage.SLDASM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]
2021-02-20 Some little changes with carriage and cables
    [BaseFrameAssembly.SLDASM, Body.SLDPRT, CableChainForXCarriage.SLDASM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]
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2021-02-22 Repaired some mates, updated cables
    [BaseFrameAssembly.SLDASM, CableChainForXCarriage.SLDASM, CableChainForYCarriage.SLDASM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]
2021-06-02 Updated the endSensor cable. Added some tolerances to parts
    [BaseFrameAssembly.SLDASM, CableChainForXCarriage.SLDASM, CableChainForYCarriage.SLDASM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]
2021-06-03 Updated the parts, made some drawings
    [BaseFrameAssembly.SLDASM, CableChainForYCarriage.SLDASM, CornerForSensor.SLDDRW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]
2021-06-05 Added some drawings. Fixed some broken mates, updated cables
    [BaseFrameAssembly.SLDASM, CableChainDriverXCarriage.SLDDRW, CableChainDriverXCarriage.SLDPRT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]
2021-07-12 Updated dimensions and tolerances. Added 2 cables for end sensors. Added drawing for the profile. Added 2 cables in the laser carriage
    [AnotherCarriageZ.SLDPRT, AssemblyCorner.SLDASM, BaseFrameAssembly.SLDASM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]
2021-07-12 Added a cable for another sensor. Added a few cables for the carriage
    [BaseFrameAssembly.SLDASM, CableChainForXCarriage.SLDASM, CableChainForYCarriage.SLDASM]
2021-07-15 Updated the stepper motor cables. Relocated the ties
    [BaseFrameAssembly.SLDASM, CableChainForYCarriage.SLDASM]
2021-07-18 Done with all cables, updated cable ties.
    [BaseFrameAssembly.SLDASM, CableChainForYCarriage.SLDASM, LaserCarriage.SLDASM]
2021-07-18 Updated links in parts properties. Updated the BOM file.
    [BaseFrameAssembly.SLDASM, CableChainForYCarriage.SLDASM, GX16-4P cable female.SLDPRT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]
2021-07-19 Updated links to materials. Updated some tolerances.
    [BaseFrameAssembly.SLDASM, CableChainForYCarriage.SLDASM, CornerForSensor.SLDPRT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]
2021-07-20 Updated parameters in parts. Renamed the Corner
    [BaseFrameAssembly.SLDASM, Carriage Y_1.SLDPRT, Carriage Y_2.SLDPRT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]
2021-07-23 Replaced all cableTies. Updated different parameters in parts. Updated DWG.NO. and PartNo parameters.
    [BaseFrameAssembly.SLDASM, CableChainForXCarriage.SLDASM, CableChainForYCarriage.SLDASM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]
2021-07-23 Updated DWG.NO. and made configuration for the 2040 profile with 402mm lenght
    [AssemblyCorner.SLDASM, BaseFrameAssembly.SLDASM, BeltLocker.SLDASM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]
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2021-08-04 Replaced almost all default nylon nuts for new ones. Made some parts as a real details. Updated some properties (DWG.NO., links, PartNo)
    [AssemblyCorner.SLDASM, BaseFrameAssembly.SLDASM, BeltLocker.SLDASM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]
2021-08-05 Replaced all default nylon nuts for new ones. Updated some properties (DWG.NO., links, PartNo)
    [BaseFrameAssembly.SLDASM, BeltLocker.SLDASM, CableChainForYCarriage.SLDASM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]
2021-08-11 Updated some parts properties. Updated some tolerances and the drawings.
    [BaseFrameAssembly.SLDASM, CableChainForXCarriage.SLDASM, CableChainForYCarriage.SLDASM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]
2021-08-16 Updated the T-slot table. Added another the profile part
    [CableChainForXCarriage.SLDASM, CableChainForYCarriage.SLDASM, LaserCarriage.SLDASM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]
2021-08-28 Updated the table assembly: added nuts and updated hole locations
    [LaserCarriage.SLDASM, LeftSideCarriage.SLDASM, Rod.SLDASM]
2021-08-28 Almost done with the table: updated a long corner, removed threads and added nuts. Updated parameters of parts and their drawings.
    [CableChainDriverXCarriage.SLDDRW, CableChainForYCarriage.SLDASM, CableChainXClamp.SLDDRW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]
2021-09-15 Added footing mount sssembly
    [BaseFrameAssembly.SLDASM, CableChainForXCarriage.SLDASM, CableChainForYCarriage.SLDASM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]
2021-11-07 Added assembly drawings for each side carriage
    [BaseFrameAssembly.SLDASM, LaserCarriage.SLDASM, LeftSideCarriage.SLDASM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]
2021-11-28 Redesigned the t-slot table. Changed the mount
    [BaseFrameAssembly.SLDASM, CableChainForXCarriage.SLDASM, CableChainForYCarriage.SLDASM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]
2021-11-28 Updated configurations in the table, updated the dimensions.
    [BaseFrameAssembly.SLDASM, CableChainForYCarriage.SLDASM, LaserCarriage.SLDASM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]
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2021-12-13 Added detailed view and label.
    [End Sensors CNC Cable.SLDDRW]
2021-12-15 Updated BOM list in the end sensors cable drawing. Added Cable label drawing.
    [Cable label.SLDDRW, End Sensors CNC Cable.SLDDRW]
2021-12-16 Added notes and updated the BOM.
    [End Sensors CNC Cable.SLDDRW]
2021-12-19 Removed some parts from the main assembly. Updated parts properties.
    [BaseFrameAssembly.SLDASM, CableChainForYCarriage.SLDASM, FoamWireCutting.SLDASM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]
2021-12-22 Updated some structure of the main assembly
    [BaseFrameAssembly.SLDASM, CableChainForXCarriage.SLDASM, CableChainForYCarriage.SLDASM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]
2022-01-06 Updated the main assembly structure
    [BaseFrameAssembly.SLDASM, CableChainForYCarriage.SLDASM, LaserCarriage.SLDASM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]
2022-01-07 Renamed some parts. Added drawing
    [BaseFrameAssembly.SLDASM, CableChainForYCarriage.SLDASM, LaserCarriage.SLDASM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]
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2022-01-15 Updated dwg numbers in the parts. Updated the main assembly structure
    [Adjustment Equipment Part.SLDPRT, BaseFrameAssembly.SLDASM, CableChain.SLDASM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]
2022-01-16 Updated screw holes in the table. Updated part names. Renumber parts & assemblies.
    [Aluminum Extrusion Table Plate T-slot.SLDPRT, BaseFrameAssembly.SLDASM, CableCarrier.SLDASM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]
2022-01-17 Replaced drawings
    [Aluminum Extrusion Table Plate T-slot.SLDDRW, Aluminum Extrusion Table Plate T-slot.SLDPRT, BaseFrameAssembly.SLDASM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]
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2022-01-22 Updated dimensions and files structure. Added more drawings
    [AssemblyCorner.SLDASM, BaseFrameAssembly.SLDASM, CableChainMountFrameX.SLDASM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]
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2022-12-24 updated parts parameters & added files for print
    [BaseFrameAssembly.SLDASM, CableChainMountFrame.SLDASM, CableChainMountFrameX.SLDASM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]
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2023-03-18 removed broken mates
    [BaseFrameAssembly.SLDASM, CableCarrier.SLDASM, DSub connector plastic cover.SLDASM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]
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
